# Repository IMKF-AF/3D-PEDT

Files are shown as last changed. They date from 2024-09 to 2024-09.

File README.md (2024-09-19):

# 3D-PEDT

***3D-Paste Extrusion Development Toolhead***

New materials are constantly being developed for additive manufacturing. Therefore, they are ideally trialled and tested in small quantities first. Particularly in the development of pastes from bio-based residues, the rapid adaptation of the material with regard to process parameters is of crucial importance.

Based on a low-cost, commercially available material extruder for plastics (MEX-TRB/P), the ***3D-PEDT*** was developed for processing pastes with the aim of minimising the work steps involved in installing the material container and keeping assembly, disassembly and cleaning as simple as possible. 
All components required for the ***3D-PEDT*** can either be manufactured with MEX-TRB/P or are available as easily accessible purchased parts. The required STL files, CAD files for the components and further porduction documents are available here as open source. 

The ***3D-PEDT*** is designed for the _Creality Ender 3 S1_,connecting parts must be adapted for other MEX-TRB/P printers. The extruder is controlled via _Klipper_ on _Repetier Server_. 

<p align="center">
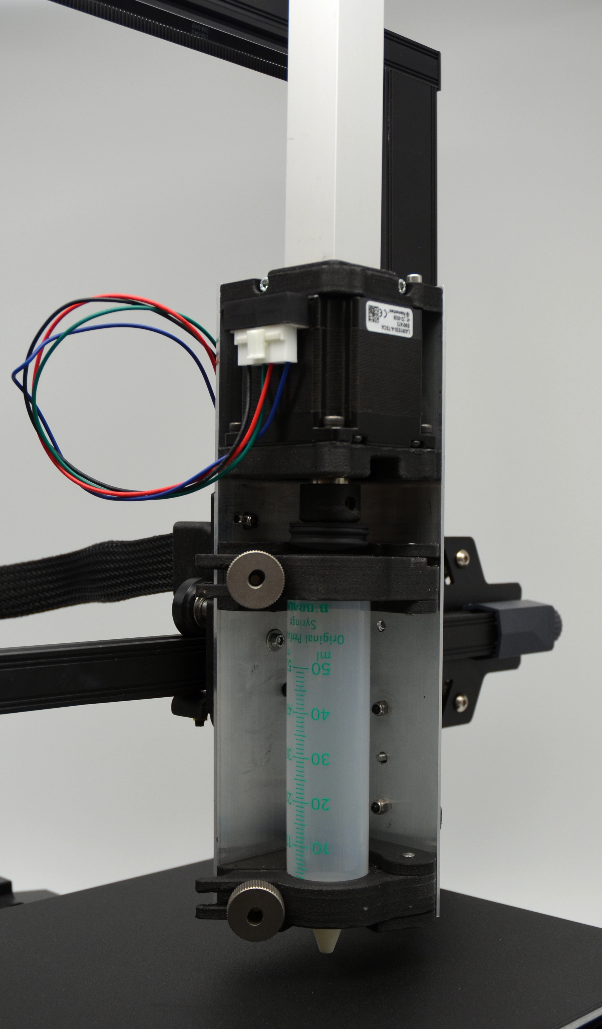
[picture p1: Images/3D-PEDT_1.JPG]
  
  
  
  
</p>

<p align="left">
  A project of the Institute for Machine Elements, Egineering Design and Manufacturing, TU Bergakademie Freiberg, Germany.
</p>

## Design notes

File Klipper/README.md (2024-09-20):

Klipper configuration file for a converted Creality Ender 3 S1

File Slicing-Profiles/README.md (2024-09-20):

Slicing Profiles for Prusa Slicer for a converted Creality Ender 3 S1 printer using the 3D-PEDT

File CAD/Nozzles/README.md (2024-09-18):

Nozzles with "_vpp_" in file name are designed to be printed with vat photopolymerisation (resin) printers.
The groves allow for drainage while printing directly on the buildplate. No support structure is needed.

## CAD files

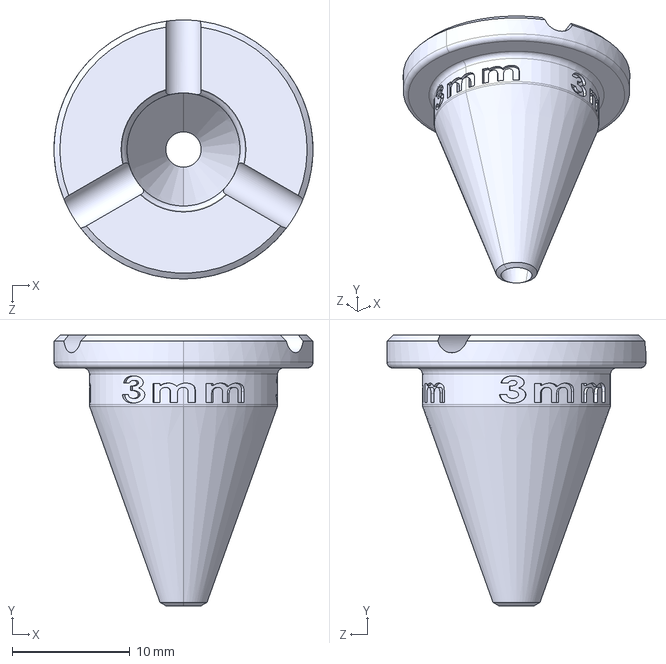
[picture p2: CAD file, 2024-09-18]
CAD/Nozzles/Nozzle_vpp_3mm.STEP
22.0 x 23.0 x 22.0 mm

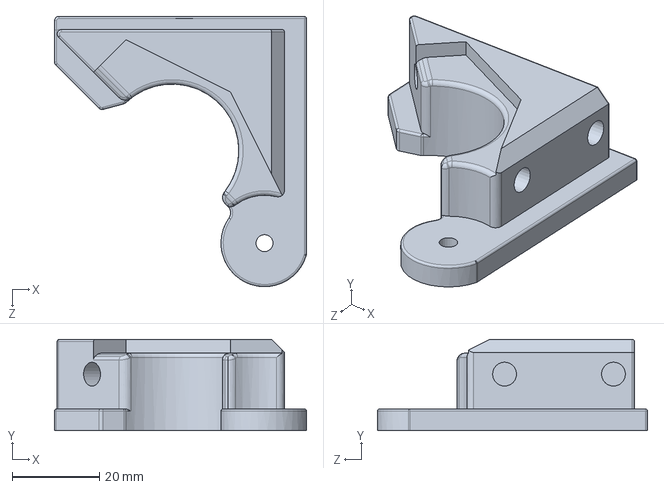
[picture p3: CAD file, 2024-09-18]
CAD/SOLIDWORKS/Upper_Syringe_Holder_Part-1.SLDPRT
57.9 x 21.0 x 62.1 mm

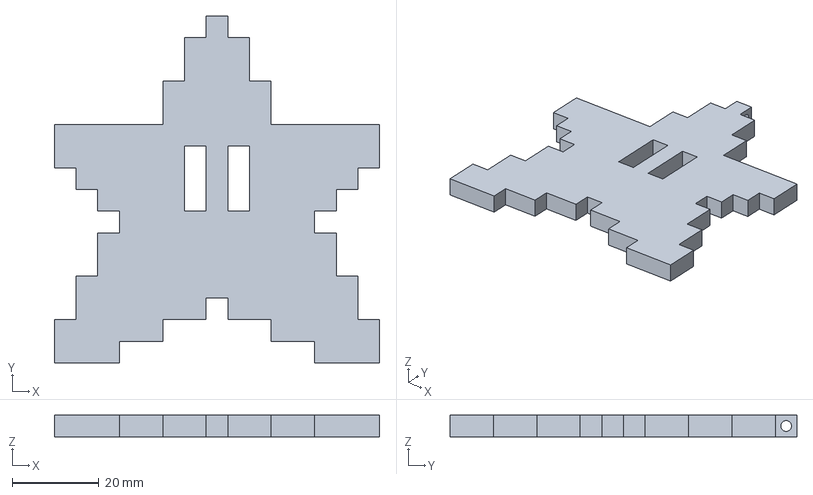
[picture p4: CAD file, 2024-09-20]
Slicing-Profiles/3D-PEDT_8mm.3mf
75.0 x 80.0 x 5.00 mm

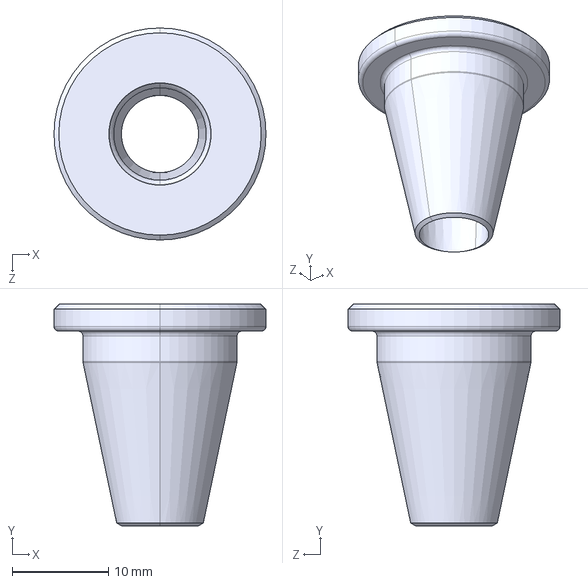
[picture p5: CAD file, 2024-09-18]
CAD/Nozzles/Nozzle_8mm.STEP
22.0 x 23.0 x 22.0 mm

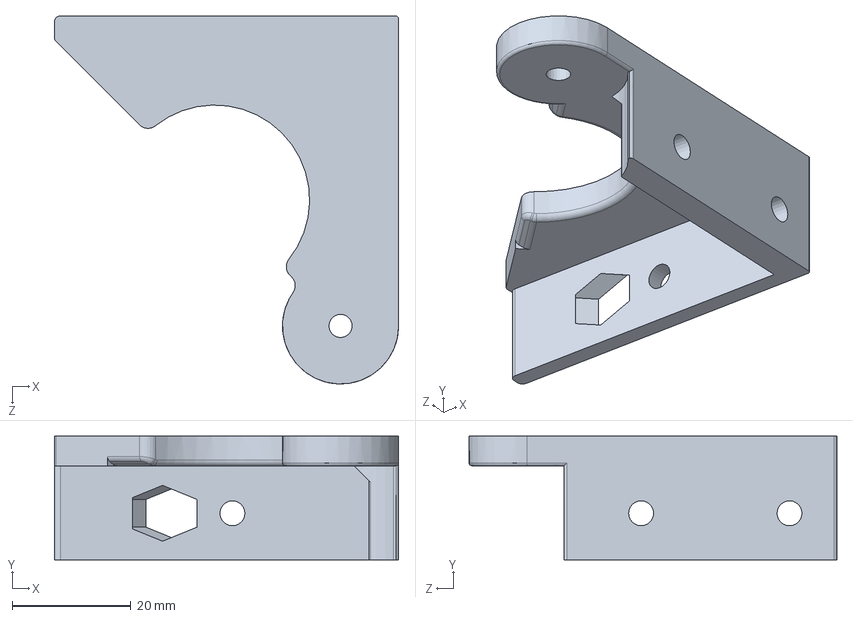
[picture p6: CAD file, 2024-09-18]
CAD/SOLIDWORKS/Upper_Syringe_Holder_Part-3.SLDPRT
58.0 x 20.9 x 62.0 mm

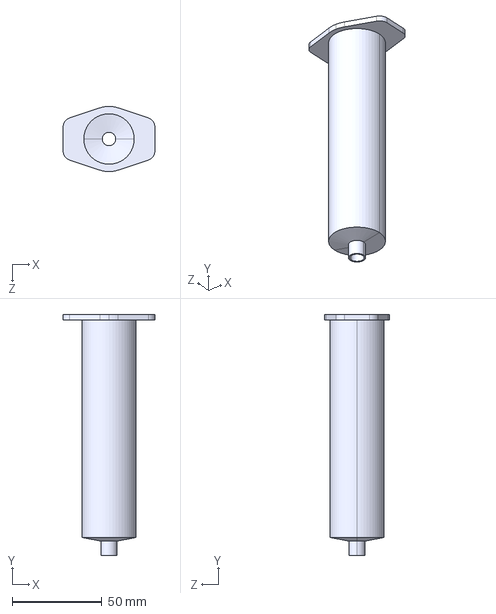
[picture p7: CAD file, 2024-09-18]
CAD/STEPs/Syringe.STEP
51.0 x 134.0 x 36.3 mm

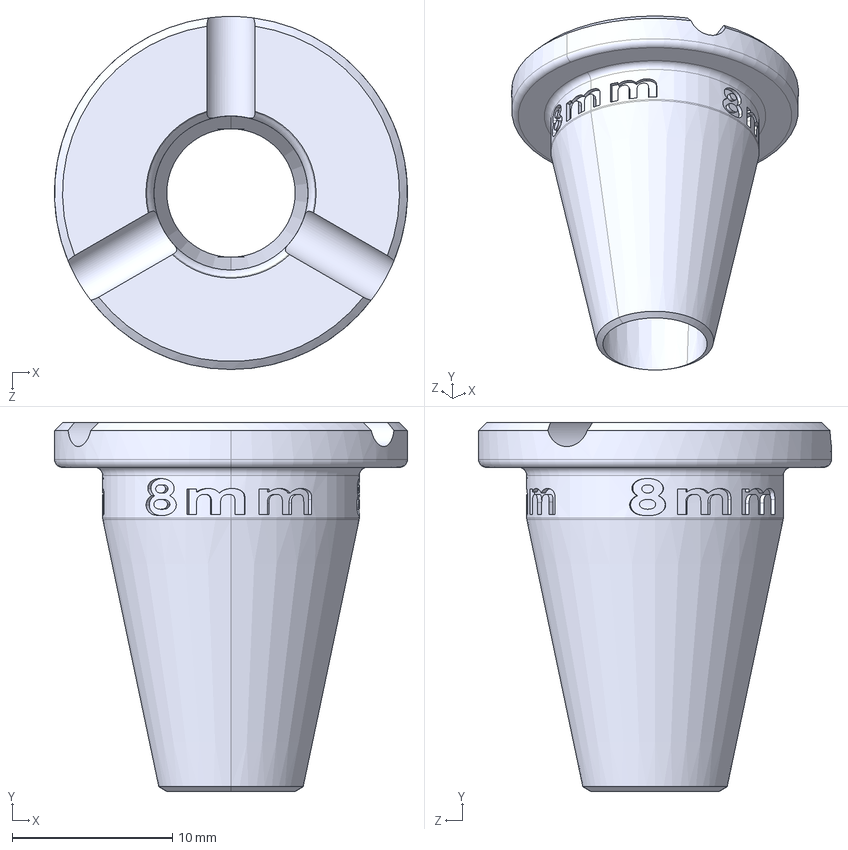
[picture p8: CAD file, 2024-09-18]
CAD/Nozzles/Nozzle_vpp_8mm.STEP
22.0 x 23.0 x 22.0 mm

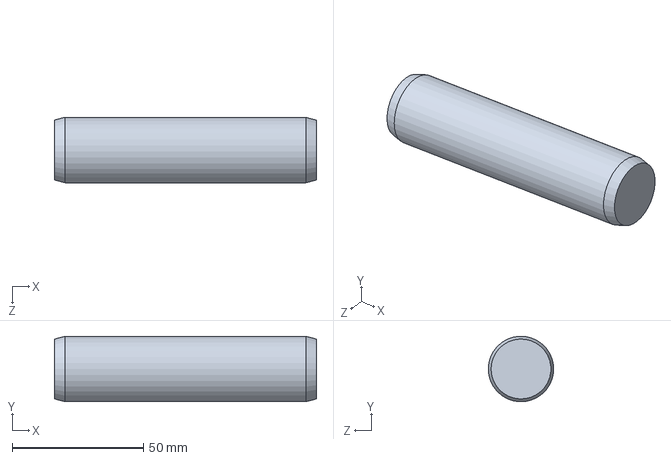
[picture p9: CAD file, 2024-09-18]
CAD/SOLIDWORKS/parallel pin unhardened_din.sldprt
100.0 x 25.0 x 25.0 mm

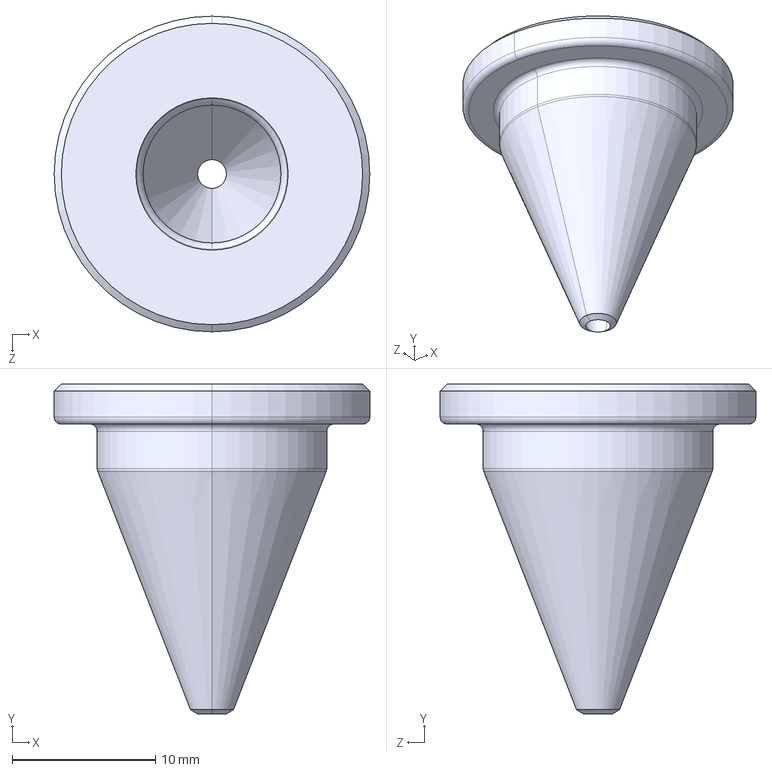
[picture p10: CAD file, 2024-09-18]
CAD/Nozzles/Nozzle_2mm.STEP
22.0 x 23.0 x 22.0 mm

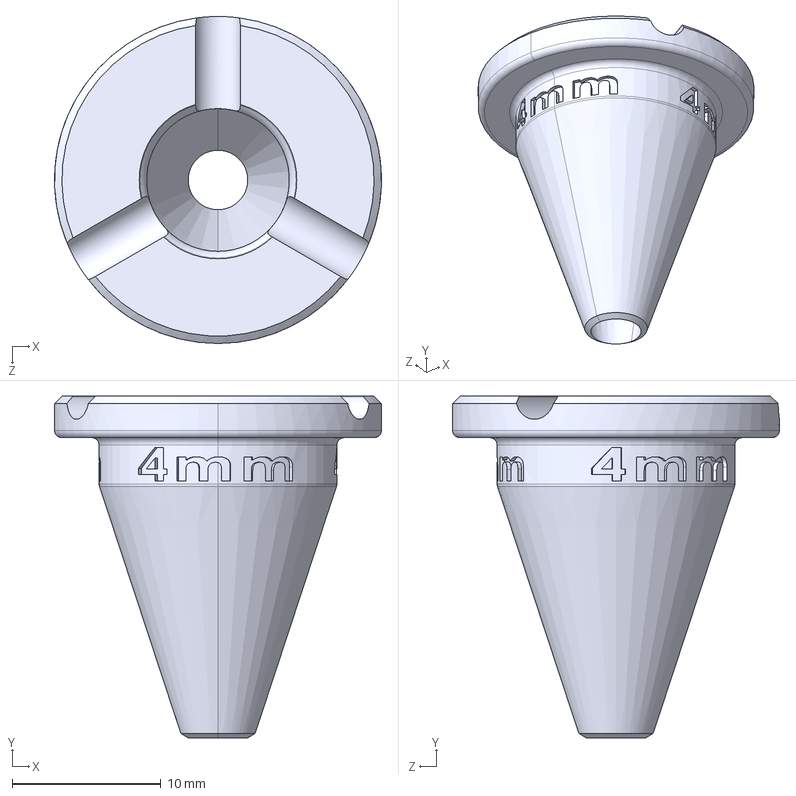
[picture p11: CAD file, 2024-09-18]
CAD/Nozzles/Nozzle_vpp_4mm.STEP
22.0 x 23.0 x 22.0 mm

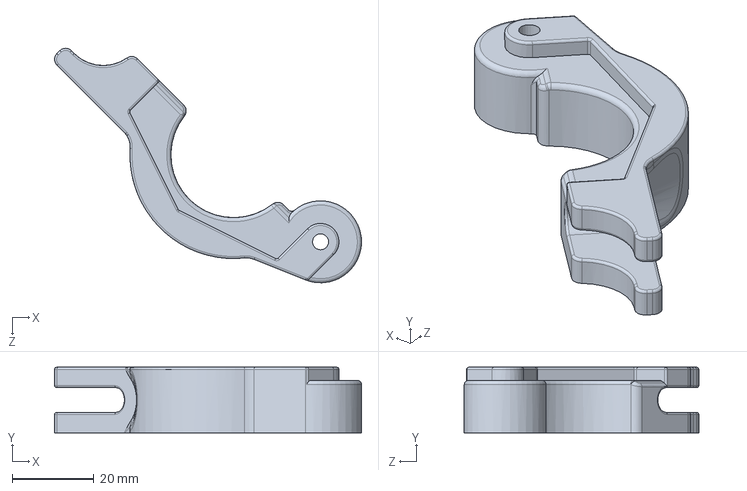
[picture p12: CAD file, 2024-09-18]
CAD/SOLIDWORKS/Upper_Syringe_Holder_Part-2.SLDPRT
74.9 x 16.0 x 57.2 mm

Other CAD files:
Slicing-Profiles/3D-PEDT_4mm.3mf
CAD/Nozzles/Nozzle_4mm.STEP
CAD/STEPs/Upper_Syringe_Holder.STEP
Slicing-Profiles/3D-PEDT_3mm.3mf
Slicing-Profiles/3D-PEDT_6mm.3mf
CAD/Nozzles/Nozzle_vpp_2mm.STEP
Slicing-Profiles/3D-PEDT_2mm.3mf
CAD/Nozzles/Nozzle_2mm.SLDPRT
CAD/Nozzles/Nozzle_2mm.STL
CAD/Nozzles/Nozzle_3mm.SLDPRT
CAD/Nozzles/Nozzle_3mm.STEP
CAD/Nozzles/Nozzle_3mm.STL
CAD/Nozzles/Nozzle_4mm.SLDPRT
CAD/Nozzles/Nozzle_4mm.STL
CAD/Nozzles/Nozzle_6mm.SLDPRT
CAD/Nozzles/Nozzle_6mm.STEP
CAD/Nozzles/Nozzle_6mm.STL
CAD/Nozzles/Nozzle_8mm.SLDPRT
CAD/Nozzles/Nozzle_8mm.STL
CAD/Nozzles/Nozzle_vpp_2mm.SLDPRT
CAD/Nozzles/Nozzle_vpp_2mm.STL
CAD/Nozzles/Nozzle_vpp_3mm.SLDPRT
CAD/Nozzles/Nozzle_vpp_3mm.STL
CAD/Nozzles/Nozzle_vpp_4mm.SLDPRT
CAD/Nozzles/Nozzle_vpp_4mm.STL
CAD/Nozzles/Nozzle_vpp_6mm.SLDPRT
CAD/Nozzles/Nozzle_vpp_6mm.STEP
CAD/Nozzles/Nozzle_vpp_6mm.STL
CAD/Nozzles/Nozzle_vpp_8mm.SLDPRT
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

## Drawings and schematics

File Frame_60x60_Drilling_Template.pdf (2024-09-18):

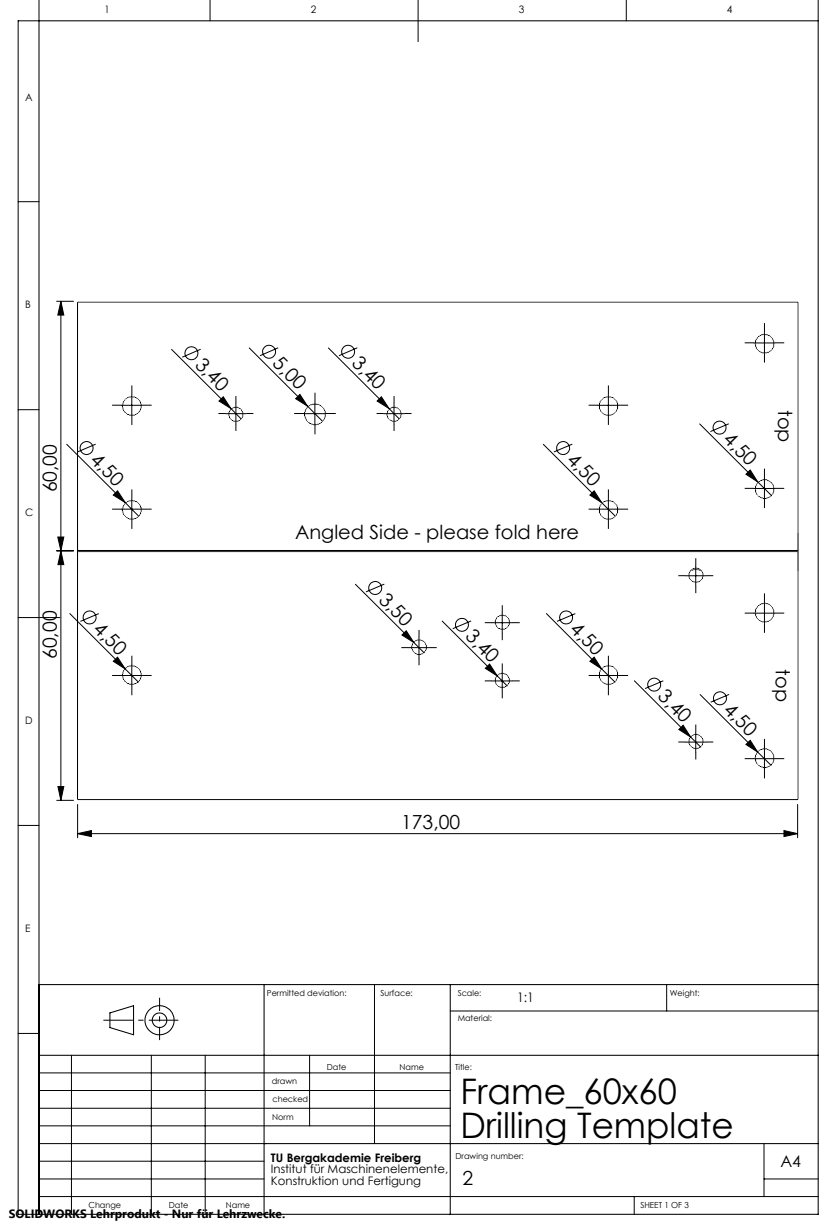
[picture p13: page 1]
Drilling Template; Permitted deviation:; Weight:; SHEET 1 OF 3; Drawing number:; Konstruktion und Fertigung

Angled Side - please fold here

TU Bergakademie Freiberg
Institut für Maschinenelemente,

SOLIDWORKS Lehrprodukt - Nur für Lehrzwecke.

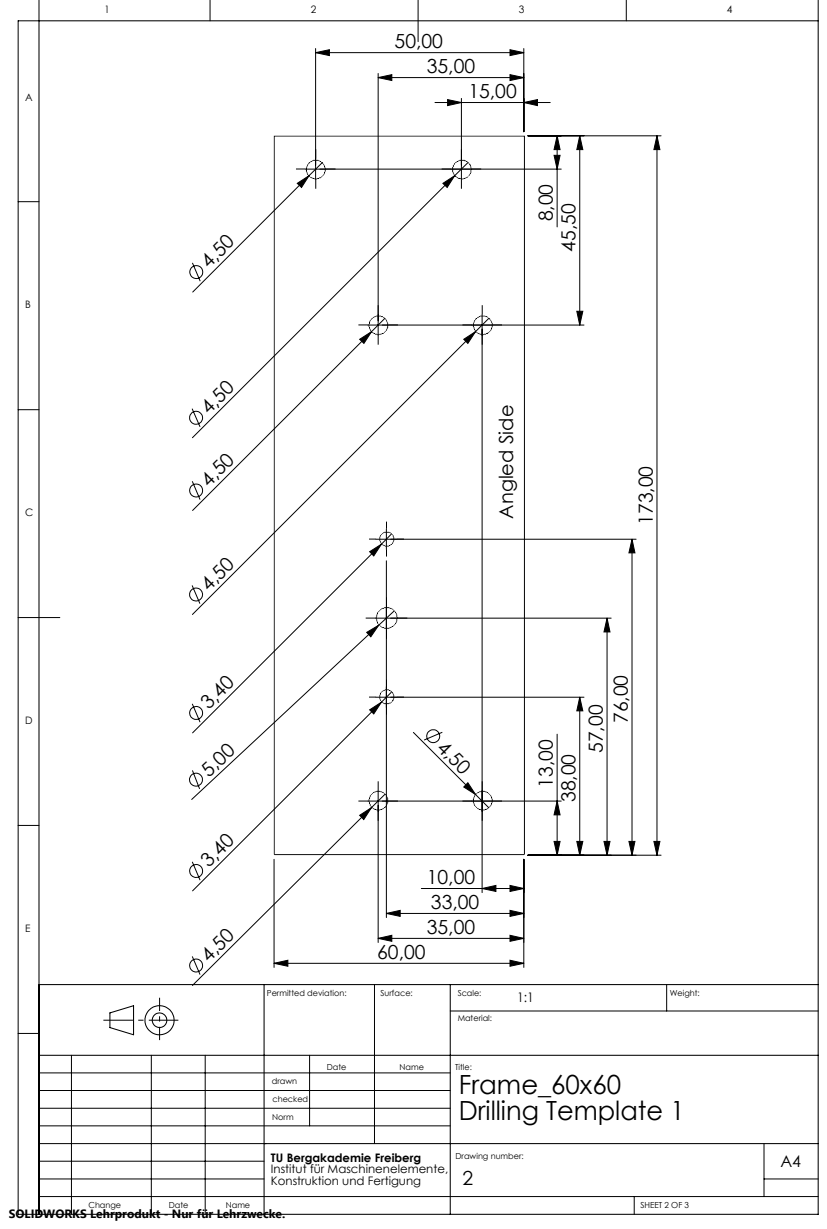
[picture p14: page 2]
Angled Side; Drilling Template 1; Permitted deviation:; Weight:

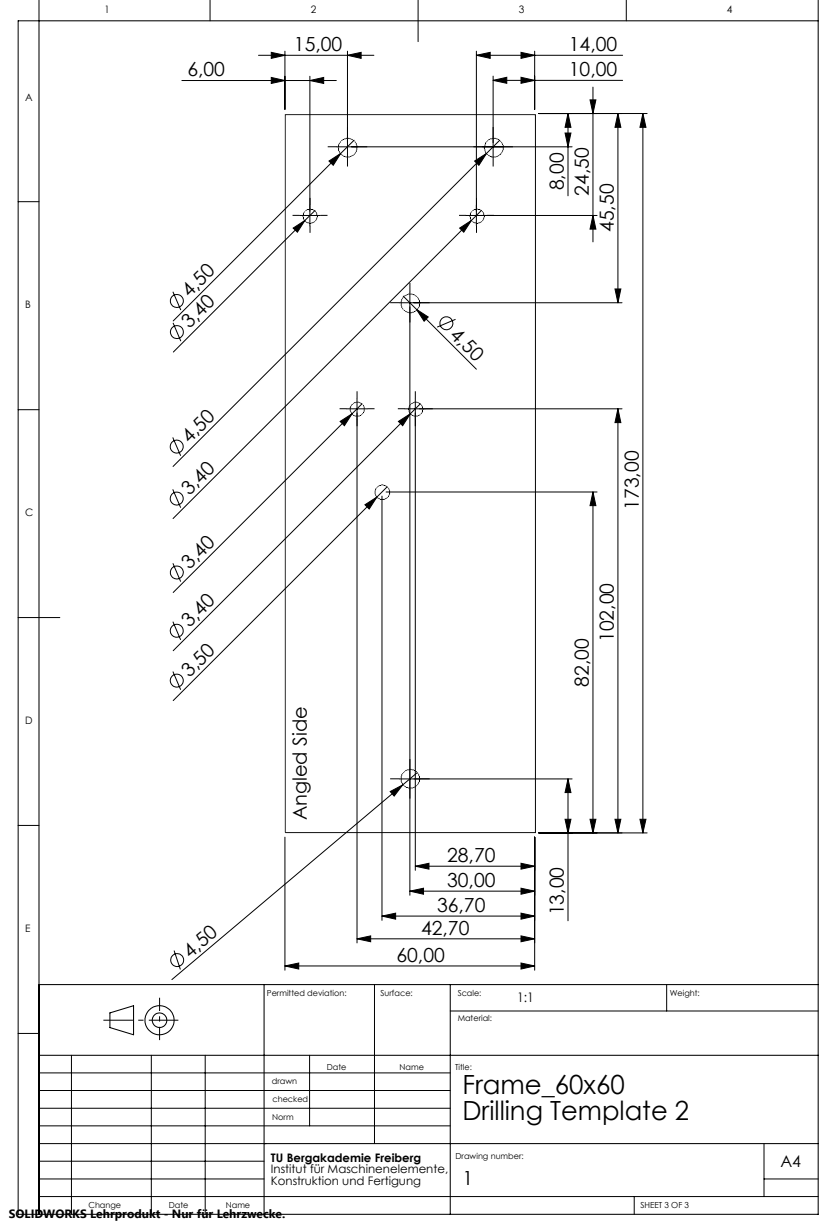
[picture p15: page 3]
Angled Side; Drilling Template 2; Permitted deviation:; Weight:

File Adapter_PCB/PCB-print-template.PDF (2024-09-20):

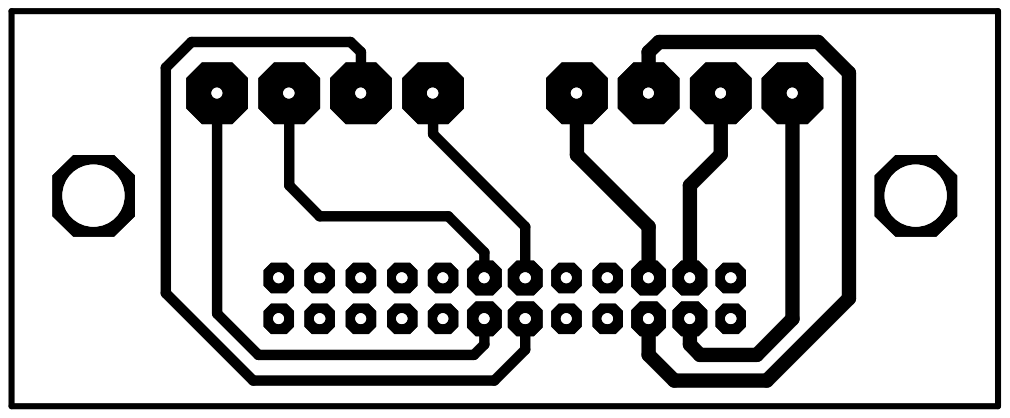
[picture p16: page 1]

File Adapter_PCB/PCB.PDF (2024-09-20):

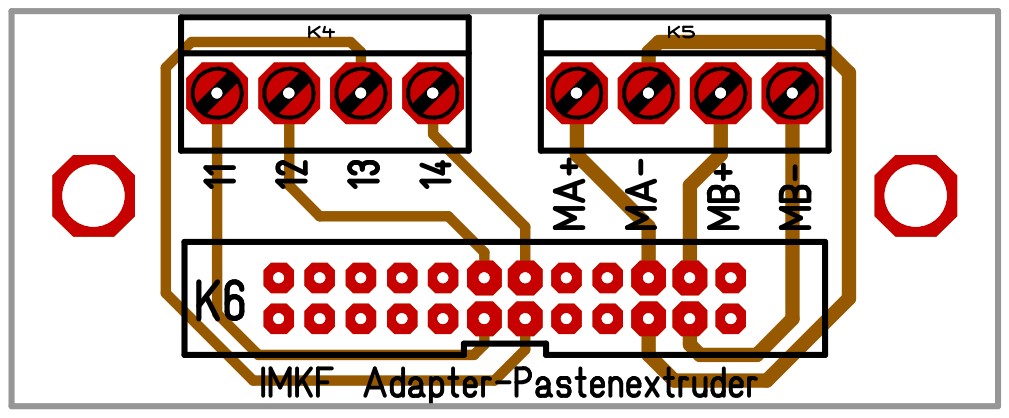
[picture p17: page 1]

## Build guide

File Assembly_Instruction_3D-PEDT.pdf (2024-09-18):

Assembly Instruction 3D-PEDT | 1/2

### Assembly Instruction 3D-PEDT - related technical drawings

Nr. | Working Step | Tools
| Preparation
1 | Deburr 3D printed components, remove brim + support structures | Deburrer or knife, files, knifes
2 | Melting threaded inserts into the components (9) (12) (20) (25) | soldering iron + tip adapter (if available)
3 | Glue the drilling template to the frame (10) and drill and deburr the holes | Drills deburrer
| Note: all screws must be fitted with washers | -

### Motor assembly

Note: designed for a shaft coupling with the outside dimensions of d = 16 mm and l = 23 mm.
Other dimensions can be used as long as they fit into the syringe and the linear guide, that maybe requires a linear
guide of a difference length and other distances of the syringe holders as well as changes to the design of the linear
guide and the piston adapter.
4 | Adjust the linear guide glider (6) to the linear guide (7), this must move smoothly (rework glider if necessary) | Files, sandpaper
5 | Mount the linear guide glider (6) on the shaft coupling (5) | allen key
6 | Mount shaft coupling (5) on the lead screw (2) | allen key
7 | Turn the lead screw (2) into the thread of the stepper motor (1) | -
8 | Fit two hexagon nuts M3 in the designated recesses of the linear guide mount (11) | -
9 | Insert the linear guide (7) into the linear guide holder (11) and clamp with two head cap screw M3 x 8 | allen key
10 | Grease the lead screw (2) the thread guide of the motor (1) | lubricant
11 | Grease the linear guide glider (6) and thread it into the linear guide (7) | lubricant
12 | Screw the linear guide mount (11) to the stepper motor (1) using four head cap screw M3 x 8 | allen key
13 | Mount the linear guide cover (8) on the linear guide (7) | -

### Upper syringe holder assembly

14 | Fit the hexagon head screw M5 x 40 (24) in the recess provided in upper syringe holder part 1 (29) | nut M5 spanner
15 | Install pin 4 h6 x 24 (23) in upper syringe holder part 2 (21) | Hammer if necessary
16 | Install upper syringe holder part 2 (21) with the pin (23) centred between part 1 (20) and part 3 (22) | Hammer if necessary

Assembly Instruction 3D-PEDT | 2/2
Nr. | Working Step | Tools
| Lower syringe holder assembly
17 | Fit the hexagon head screw M5 x 40 (24) in the recess provided in lower syringe holder part 1 (25) | -
18 | Install pin 4 h6 x 24 (23) in lower Syringe Holder part 2 (26) | Hammer if necessary
19 | Install lower syringe holder part 2 (26) with the pin (23) centred between part 1 (25) and part 3 (27) | Hammer if necessary

### Syringe holder assembly

20 Mount the lower syringe holder group (25, 26, 27) to the frame (10) using two head cap screws M4 x 12 and one head | cap screws M4 x 8 | allen key
21 | Mount the stepper motor mount (9) to the frame (10) using four head cap screws M4 x 8 | allen key
22 | Mount the lower syringe holder group (20, 21, 22) to the frame (10) using three head cap screws M4 x 12 | allen key
23 To align the upper and lower syringe holder, install a syringe (17) and secure it with the quick-release knurled nuts (16). | Tighten the screws of the upper and lower syringe holder firmly | allen key
24 If available, fit additional touch sensor mount (12), spacer (14) and cable mount (15). These components are specific to | the “base machine” used and must be adapted accordingly. | allen key

### Piston assembly

25 | Mount the piston adapter (13) to the shaft coupling (4) | allen key
26 | Mount the shaft coupling (4) to the lead screw (2) using two head cap screws M3 x 8 | allen key
27 | Place the rubber piston (18) on the piston adapter (13) | -

### Extruder assembly group

28 Connect the motor assembly to the syringe holder assembly by mounting the stepper motor (1) on the stepper motor | holder (9) with three head cap screws M4 x 16 and one M4 x 25. To centre the stepper motor, push the piston completely into the syringe before tightening the screws. | allen key
29 | Connect the cable to control the motor and possibly the touch sensor | screwdriver

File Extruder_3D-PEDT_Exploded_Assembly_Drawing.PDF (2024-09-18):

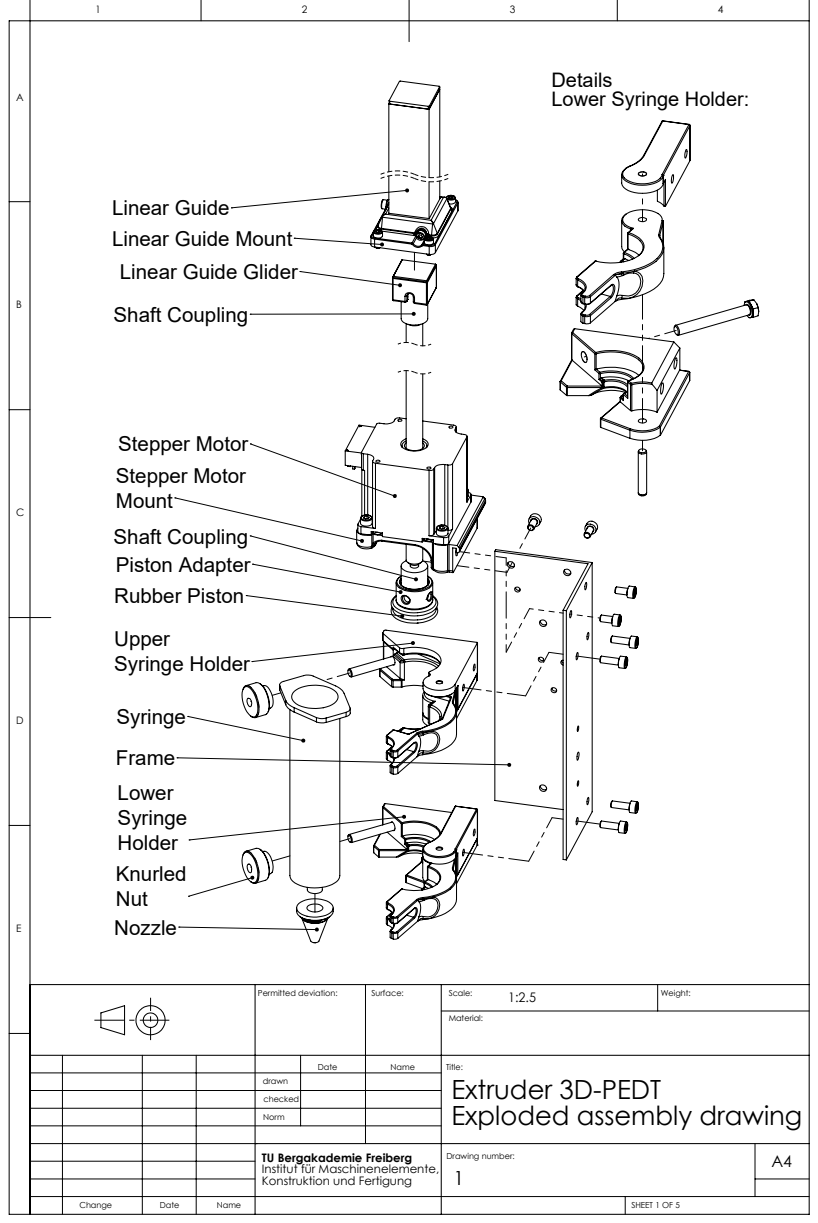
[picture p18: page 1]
Rubber Piston; Syringe Holder; Piston Adapter; Stepper Motor Stepper Motor; Shaft Coupling; Permitted deviation:; Weight:; SHEET 1 OF 5; Drawing number:; Konstruktion und Fertigung

Details
Lower Syringe Holder:

Linear Guide
Linear Guide Mount
Linear Guide Glider
Shaft Coupling

Material:
Extruder 3D-PEDT
Exploded assembly drawing

TU Bergakademie Freiberg
Institut für Maschinenelemente,

37 | 4 | ISO 7040-M3-N | hexagon nut with clamping part
36 | 4 | Hexagon Nut ISO 4032 - M3 - W - N | hexagon nut (2 of them printer specific)
35 | 9 | DIN 912 M3 x 8 --- 8N | hexagon socked head cap screw
34 | 1 | DIN 912 M3 x 10 --- 10N | hexagon socked head cap screw (printer specific)
33 | 2 | DIN 912 M3 x 12 --- 12N | hexagon socked head cap screw
32 | 2 | DIN 912 M3 x 16 --- 16N | hexagon socked head cap screw (printer specific)
31 | 3 | DIN 912 M4 x 25 --- 25N | hexagon socked head cap screw
30 | 1 | DIN 912 M4 x 16 --- 16N | hexagon socked head cap screw
29 | 6 | DIN 912 M4 x 12 --- 12N | hexagon socked head cap screw
28 | 4 | DIN 912 M4 x 8 --- 8N | hexagon socked head cap screw
27 | 1 | Lower_Syringe_Holder_Part-3 | AM part
26 | 1 | Lower_Syringe_Holder_Part-2 | AM part
25 | 1 | Lower_Syringe_Holder_Part-1 | AM part
24 | 2 | DIN EN 24014 - M5 x 40 x 16-N | hexagonal bolt with shank
23 | 2 | Parallel Pin ISO 2338 - 4 h6 x 24 - St | cylindrical pin
| 22 | 1 | Upper_Syringe_Holder_Part-3 | AM part
| 21 | 1 | Upper_Syringe_Holder_Part-2 | AM part
| 20 | 1 | Upper_Syringe_Holder_Part-1 | AM part
| 19 | 1 | Nozzle_4mm | AM part
| 18 | 1 | Rubber_Piston | B. Braun 50 ml Perfusor syringe without cannula, Art. No. 131246
| 17 | 1 | Syringe | B. Braun 50 ml Perfusor syringe without cannula, Art. No. 131246
| 16 | 2 | Knurled_Nut_GN-6303.1-M5-NI | with quick-release function, M5
| (15) | 1 | Cable_Mount | AM part, printer specific
| (14) | 1 | Spacer_Printer_Linear_x-Axis | AM part, printer specific
| 13 | 1 | Piston_Adapter | AM part
| (12) | 1 | Touch_Sensor_Mount | AM part, printer specific
| 11 | 1 | Linear_Guide_Mount | AM part
| 10 | 1 | Frame_60x60 | aluminium angle 60mm x 60mm x 2mm, l = 173 mm, anodised
| 9 | 1 | Stepper_Motor_Mount | AM part
| 8 | 1 | Linear_Guide_Cover | AM part
| 7 | 1 | Linear_Guide | aluminium square profile, 25mm x 25mm x 1.5mm, l = 173mm, anodised
| 6 | 1 | Linear_Guide_Glider | AM part
| 5 | 1 | Shaft_Coupling | rigrid, 10mm x 10mm (outside: d=16 mm, l=23 mm)
| 4 | 1 | Shaft_Coupling | rigrid, 5mm x 10mm (outside: d=16 mm, l=23 mm)
| 3 | 1 | Motor_Cable | ZK-VHR-6-300-4, SCA56, 0.3 m
| 2 | 1 | Lead_Screw_Tr10x2_200 | SCREW-ABA_TSCA-200, stainless steel
| 1 | 1 | Stepper_Motor_Nema_23 | LA561S20-A-TSCA - non captive linear actuator, Nema 23
| ITEM | QTY | Name | Description

C

B

D

E

# Extruder 3D-PEDT Parts list

Permitted deviation: | Weight:

Title:

Material:

Date

Name

Surface:

Norm

drawn
checked

Scale:

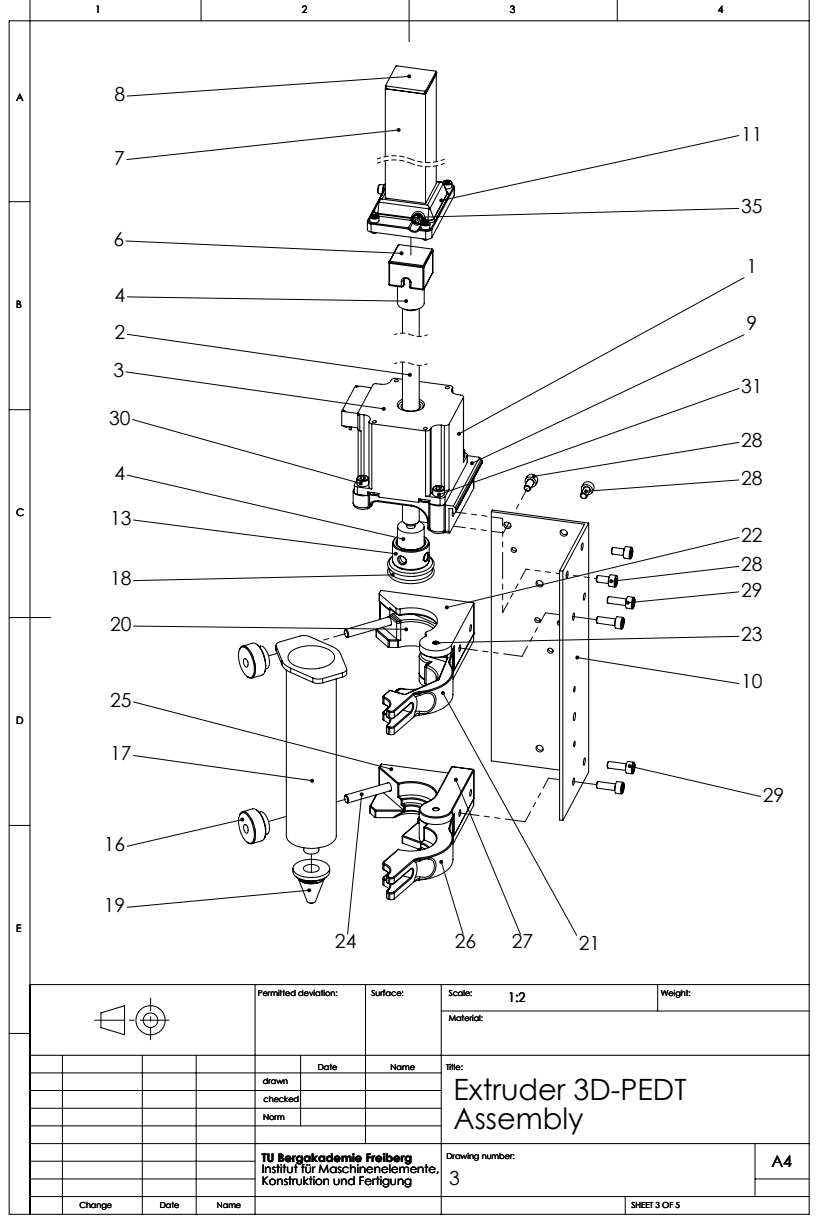
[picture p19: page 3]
Permitted deviation:; Weight:; Extruder 3D-PEDT

Konstruktion und Fertigung

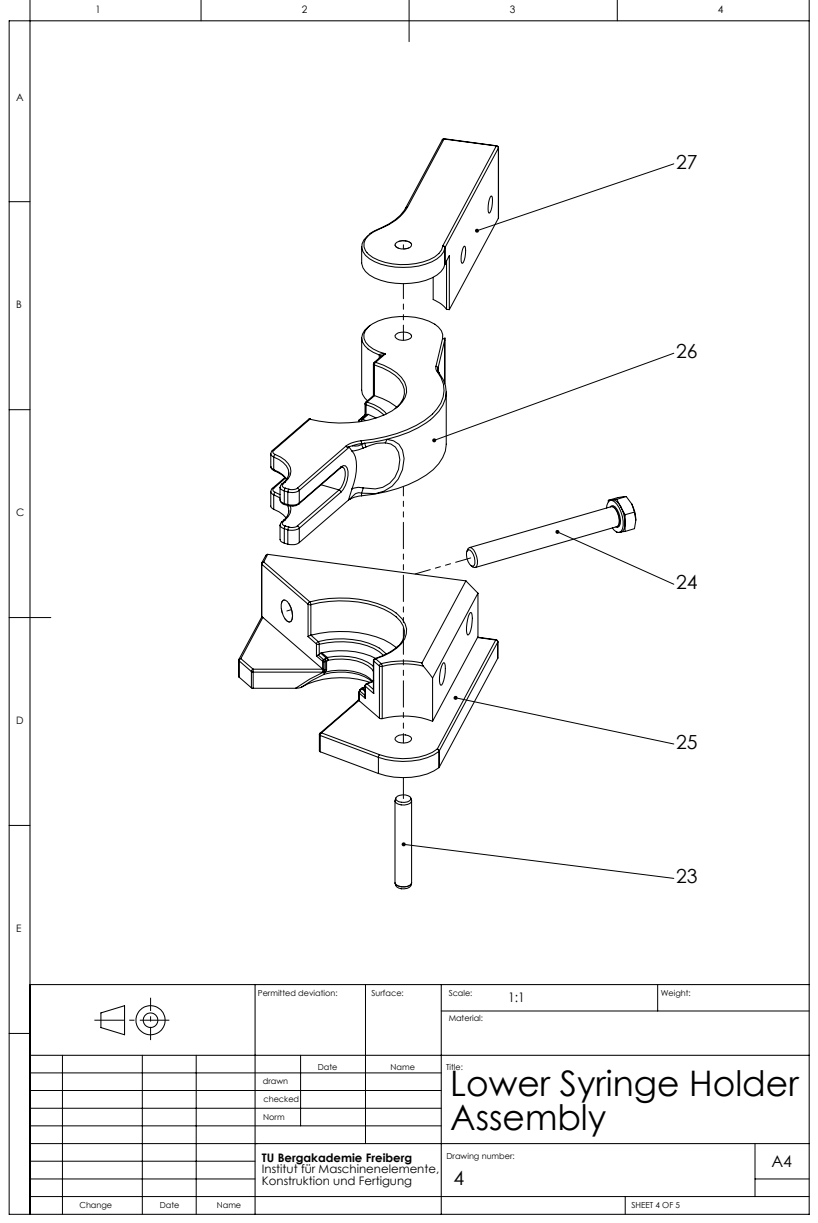
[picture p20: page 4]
Permitted deviation:; Weight:

Surface:
Lower Syringe Holder
Title:
Assembly

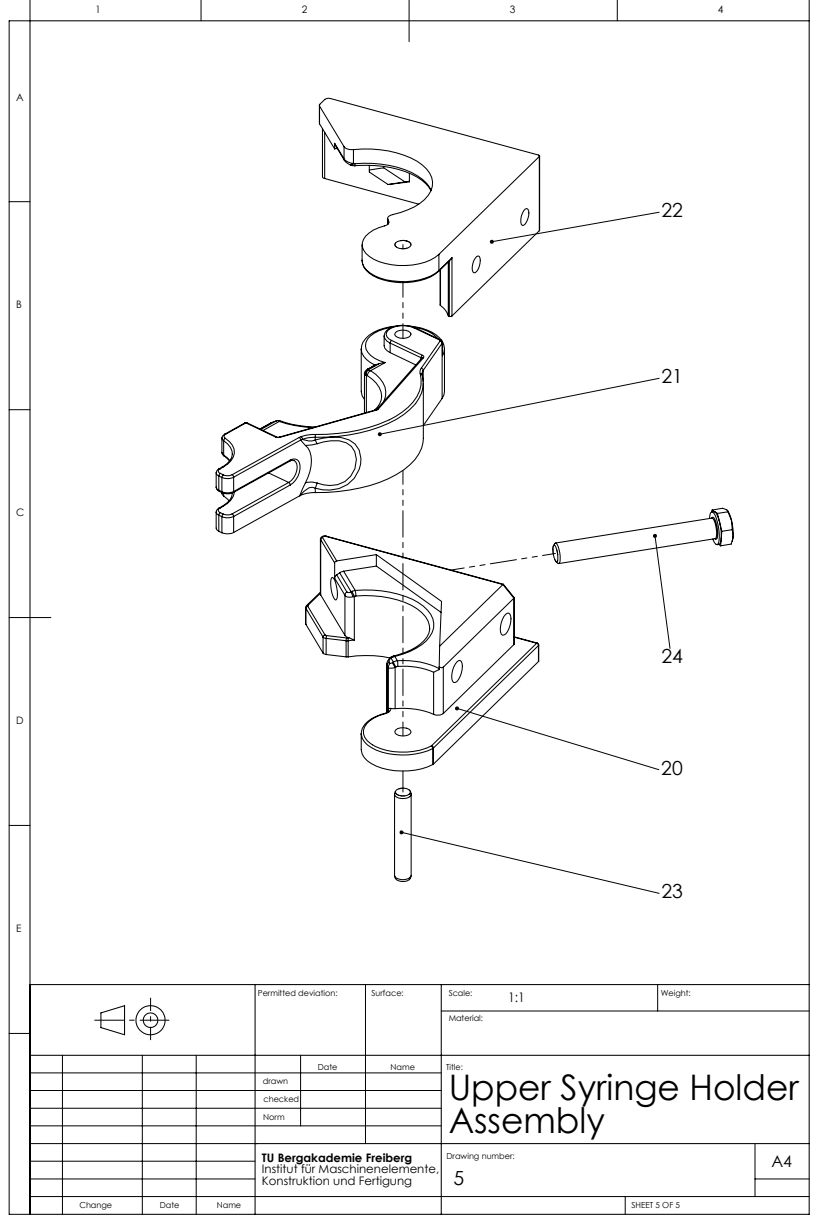
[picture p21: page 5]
Permitted deviation:; Weight:

Surface:
Upper Syringe Holder
Assembly

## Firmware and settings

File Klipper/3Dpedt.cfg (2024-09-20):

# This is the configuration for the printer: Creality Ender 3 S1 with the 3D-PEDT conversion
# This option is needed if you want to use the recover feature so that Repetier-Server can manually set the z position in Klipper
#[force_move]
#enable_force_move: true

# This file contains pin mappings for the stock 2021 Creality Ender 3
# S1 & S1 Pro. To use this config, check the STM32 Chip on the
# Mainboard, during "make menuconfig" select accordingly either the
# STM32F103 with "28KiB bootloader" or the STM32F401 with
# "64KiB bootloader" and serial (on USART1 PA10/PA9) for both.

# For a direct serial connection, in "make menuconfig" select
# "Enable extra low-level configuration options" and  Serial
# (on USART2 PA3/PA2), which is on the 10 pin IDC cable used
# for the LCD module as follows: 3: Tx, 4: Rx, 9: GND, 10: VCC

# Flash this firmware by copying "out/klipper.bin" to a SD card and
# turning on the printer with the card inserted. The filename
# must be changed to "firmware.bin"

# With STM32F401, you might need to put "firmware.bin" in a
# folder on the SD card called "STM32F4_UPDATE" in order to flash.

# See docs/Config_Reference.md for a description of parameters.

[stepper_x]
step_pin: PC2
dir_pin: PB9
enable_pin: !PC3
microsteps: 16
rotation_distance: 40
endstop_pin: !PA5
position_endstop: -18
position_max: 225
position_min: -18
homing_speed: 150
homing_retract_dist: 5
homing_retract_speed: 150
second_homing_speed: 10

[stepper_y]
step_pin: PB8
dir_pin: PB7
enable_pin: !PC3
microsteps: 16
rotation_distance: 40
endstop_pin: !PA6
position_endstop: -29
position_max: 210
position_min: -29
homing_speed: 150
homing_retract_dist: 5
homing_retract_speed: 150
second_homing_speed: 10

[stepper_z]
step_pin: PB6
dir_pin: !PB5
enable_pin: !PC3
microsteps: 16
rotation_distance: 8
endstop_pin: probe:z_virtual_endstop
position_max: 210
position_min: -2.5
homing_speed: 20
homing_retract_dist: 2
homing_retract_speed: 20
second_homing_speed: 2

[extruder]
step_pin: PB4
dir_pin: PB3
enable_pin: !PC3
microsteps: 16
gear_ratio: 1:1
rotation_distance: 2
nozzle_diameter: 4.00
filament_diameter: 28.00
heater_pin: PA1
sensor_type: EPCOS 100K B57560G104F
sensor_pin: PC5
control: pid
pid_Kp: 23.561
pid_Ki: 1.208
pid_Kd: 114.859
min_temp: -273
max_temp: 9999999 # Set to 300 for S1 Pro
min_extrude_temp: -273
max_extrude_only_velocity: 7.5
max_extrude_only_accel: 50

[heater_bed]
heater_pin: PA7
sensor_type: EPCOS 100K B57560G104F
sensor_pin: PC4
control: pid
pid_Kp: 71.867
pid_Ki: 1.536
pid_Kd: 840.843
min_temp: 0
max_temp: 100 # Set to 110 for S1 Pro

[heater_fan hotend_fan]
pin: PC0

[fan]
pin: PA0

[mcu]
#serial: /dev/serial/by-id/usb-1a86_USB_Serial-if00-port0
serial: /dev/serial/by-id/usb-1a86_USB_Serial-if00-port0
restart_method: command

[printer]
kinematics: cartesian
max_velocity: 250
max_accel: 5000
max_z_velocity: 30
max_z_accel: 100

[bltouch]
sensor_pin: ^PC14
control_pin: PC13
x_offset: 48
y_offset: 0
z_offset: 2.5
probe_with_touch_mode: true
stow_on_each_sample: false

[bed_mesh]
speed: 250
mesh_min: 48 , 48
mesh_max: 177, 162
probe_count: 3,3
algorithm: bicubic


[safe_z_home]
home_xy_position: 67.5,105
speed: 150
z_hop: 5
z_hop_speed: 20
move_to_previous: true

[filament_switch_sensor e0_sensor]
switch_pin: !PC15
pause_on_runout: true
runout_gcode: PAUSE

[pause_resume]
recover_velocity: 25

[bed_screws]
screw1: 20, 29
screw2: 195, 29
screw3: 195, 198
screw4: 20, 198

#*# <---------------------- SAVE_CONFIG ---------------------->
#*# DO NOT EDIT THIS BLOCK OR BELOW. The contents are auto-generated.
#*#
#*# [bed_mesh default]
#*# version = 1
#*# points =
#*# 	  0.012500, -0.027500, 0.057500
#*# 	  0.057500, -0.005000, 0.055000
#*# 	  0.027500, 0.002500, 0.092500
#*# x_count = 3
#*# y_count = 3
#*# mesh_x_pps = 2
#*# mesh_y_pps = 2
#*# algo = bicubic
#*# tension = 0.2
#*# min_x = 48.0
#*# max_x = 177.0
#*# min_y = 48.0
#*# max_y = 162.0
#*#
#*# [bed_mesh p1]
#*# version = 1
#*# points =
#*# 	  0.012500, -0.027500, 0.057500
#*# 	  0.057500, -0.005000, 0.055000
#*# 	  0.027500, 0.002500, 0.092500
#*# x_count = 3
#*# y_count = 3
#*# mesh_x_pps = 2
#*# mesh_y_pps = 2
#*# algo = bicubic
#*# tension = 0.2
#*# min_x = 48.0
#*# max_x = 177.0
#*# min_y = 48.0
#*# max_y = 162.0

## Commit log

2024-08-15 Create CAD
2024-08-15 upload nozzle model
    [Nozzle_4mm.SLDPRT, Nozzle_4mm.STEP]
2024-09-18 upload of all nozzles
    [Nozzle_2mm.SLDPRT, Nozzle_2mm.STEP, Nozzle_2mm.STL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]
2024-09-18 upload of all cad files
    [Cable_Mount.SLDPRT, Cable_Mount.STEP, Extruder_3D-PEDT.SLDASM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]
2024-09-20 last changes
    [3D-PEDT_2mm.3mf, 3D-PEDT_3mm.3mf, 3D-PEDT_4mm.3mf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]
2024-09-20 upload Klipper config + PCB files
    [3Dpedt.cfg]
